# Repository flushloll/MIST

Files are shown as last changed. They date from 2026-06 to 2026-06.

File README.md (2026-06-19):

# MIST
MIST is a robot in the form of a rice-cooker with legs, originating from the Pantheon Show. Our goal in this project was to test our skills whilst making something beautiful. 

This is our Zine for fallout hackathon:
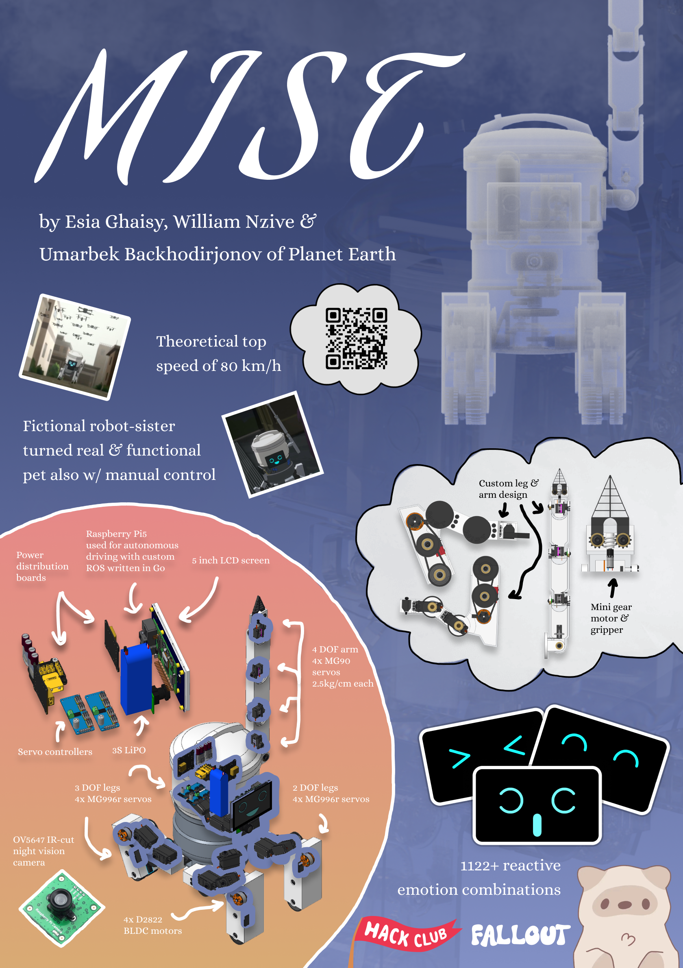
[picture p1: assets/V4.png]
Zine


This zine is the original one. (We left it here because we really liked the design and believed it deserves to be in readme at least)
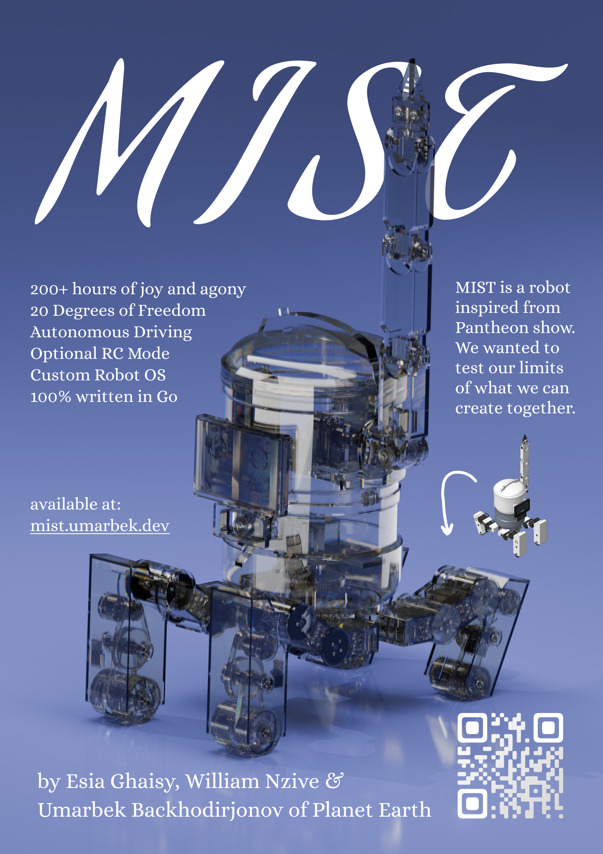
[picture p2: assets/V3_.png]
Zine 2


## Replication
All of the instructions on recreating MIST to keep as a speedy robot pet for yourself are provided below.

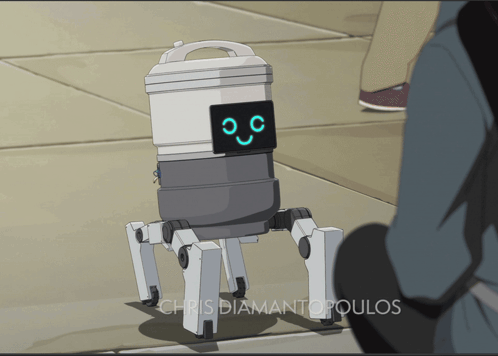
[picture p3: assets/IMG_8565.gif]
mist_gif


### Software

#### 1. Operating System
We've chosen DietPi due to its stability and in order to maximise available resources by ditching the GUI. It would be preferarble to flash some ssd instead of a flash card for reliability. In installation of the DietPi on the raspberry pi, we must choose to install these programs: tailscale, openssh, go.

#### 2. Remote control with Tailscale (optional but recommended)
```bash
# Authentication
tailscale up

# Port Forwarding
echo 'net.ipv4.ip_forward = 1' | sudo tee -a /etc/sysctl.conf 
echo 'net.ipv6.conf.all.forwarding = 1' | sudo tee -a /etc/sysctl.conf
sudo sysctl -p

# Once you've connected your pi to the network, you can ssh into it from your personal computer with these commands:
ssh username@tailscale-ip
# You can also use device name given or chosen in tailscale:
ssh username@device-name
```

#### 3. Adding GOPATH to $PATH
```bash
# 
nano ~/.bashrc

# Write these into the file:
export GOPATH=$HOME/go
export PATH="$PATH:$GOPATH/bin"
# Exit nano, and save the changes.

# Apply changes
source ~/.bashrc
```

#### 4. Installing text to voice (espeak)
```bash
# Configure audio drivers:
dietpi-config
# > Select '2: Audio Options'
# > For the 'Sound card', select 'rpi-bcm2835-hdmi' or 'usb-dac' depending on your speaker.

# Install text to speech module:
apt update
sudo apt install espeak-ng -y
```

#### 6. Setting up ollama (embeddinggemma)
```bash
# Install Ollama
sudo apt-get install zstd
curl -fsSL https://ollama.com/install.sh | sh

# Get the model
ollama pull embeddinggemma
```

#### 7. Setting up mist-os
Note that mist-os isn't an actual operating system, but rather just a program.
```bash
# Install mist-os:
go install https://github.com/flushloll/MIST/mist-os/main.go

# Run mist-os:
mist-os

# Stop:
Ctrl + C
```

Optional: If you wish to start mist-os after boot automatically:
```bash
# Find where mist-os is installed:
which mist-os
# > Please remember the path or save it to clipboard

# Open Configuration menu:
dietpi-autostart
# > Select "Custom script (background, no autologin)"
# > Press OK
# DietPi should automatically open an editable text file, otherwise open it:
nano /var/lib/dietpi/dietpi-autostart/custom.sh
# > Paste this into the file:
/root/go/bin/mist-os # paste the path given from `which matetra-client` command.
exit 0
# > Save everything, and exit
```

### Hardware

I would suggest assembling the robot by virtue of the subassemblies in the CAD, starting with the smallest and working up to the largest.

An order like this is good:
1. Chunky-Leg
2. Chunky-Leg-2
3. Skinny-Leg
4. Skinny-Leg-2
5. Rice-Cooker-Lower
6. Rice-Cooker-Center
7. Rice-Cooker-Lid
8. Arm

Keep in mind that if a part is not on the BOM then it is a 3D printed part.
Every 3D printed part is printed in PLA except the nylon_heat_brick part which is printed in nylon filament as well as the small_sleeve_1, small_sleeve_2, big_sleeve_1, and big_sleeve_2 parts which are printed in SEBS filament.

Remember to assemble the electronics and hardware as you go through this order. Everything you need to know to assemble MIST succesfully is on the CAD model.

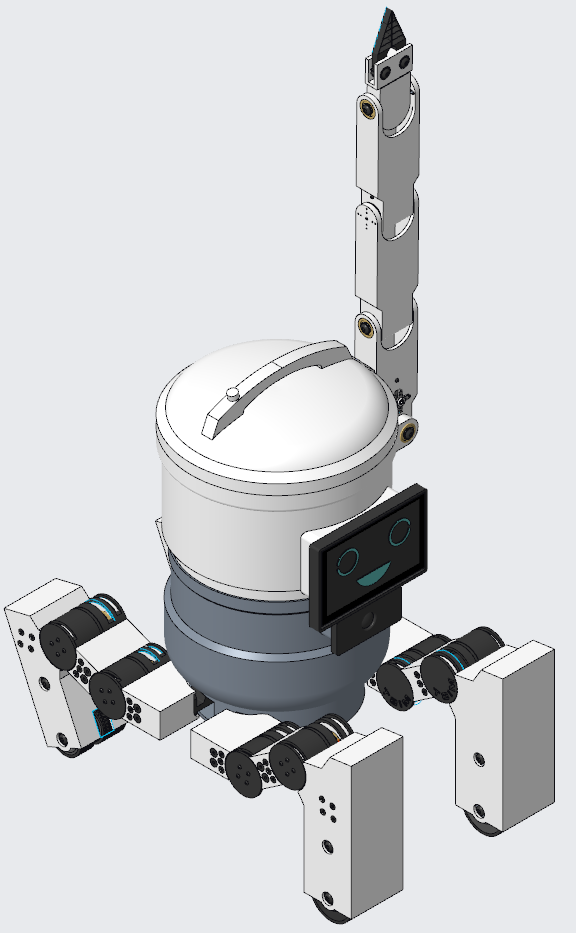
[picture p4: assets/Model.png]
Model

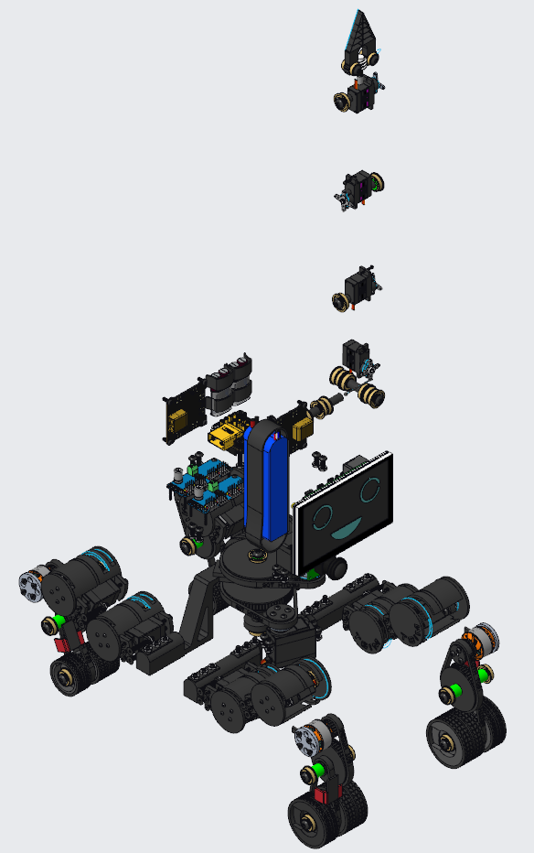
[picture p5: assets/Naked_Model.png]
Naked Model


## 1. BOM - Bill of Materials

<h3><a href="/BOM.pdf">BOM PDF</a></h3>

<h3><a href="BOM.csv">BOM CSV</a></h3>

#### 2. Electronics Wiring Guide

Here are the schematics for wiring MIST. When actually wiring MIST physically, consider where you place your wires and ensure no wires will be pinched or sliced. Use mounting tape to secure your wires onto MIST's chassis and use electrical tape and shrink tubing to cover exposed wires.

If you have questions on how to perform certain electrical tasks such as soldering, crimping, using shrink tube & electrical tape, cutting wire, and just splicing wire in general then please research how to do so before working on MIST. MIST can produce currents capable of setting fire or frying electronics. If you are unsure of how to manage these currents through programming then it would be wise to integrate physical fuses in between electronics to prevent accidents. When deciding on where fuses can be integrated in your circuit consider the maximum current passing through a segment and use that number to decide on the current limit of your fuse. [Here's a good starting point on how to get started with fuses:](https://community.element14.com/technologies/experts/w/documents/27978/a-comprehensive-guide-to-fuses)

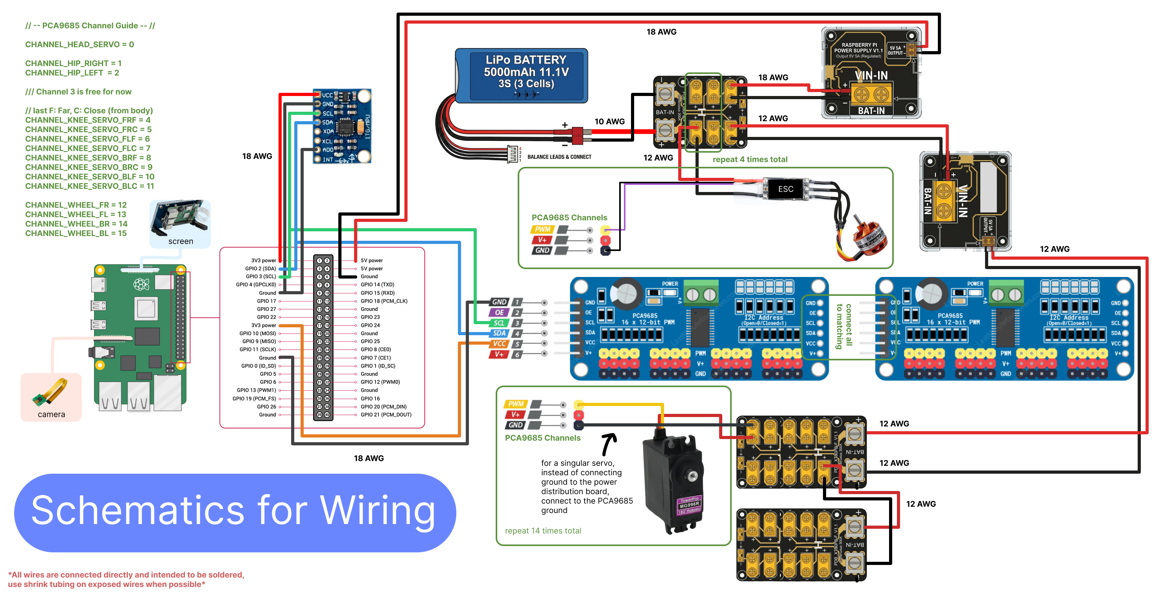
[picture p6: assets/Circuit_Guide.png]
Circuit Guide


#### 3. Enable I2C & Components Test
```zsh
# Open the configuration menu:
dietpi-config
# > Navigate to 'Advanced Options',
# > Ensure 'I2C state' is selected as 'On',
# > Ensure 'I2C frequency' is set to 100 kHz,
# > Exit and reboot the raspberry pi.

# To see if your IMU module is connected, run:
sudo i2cdetect -y 1
# 0x4b is IMU
# ____ is PCA9685
```

# Contribute
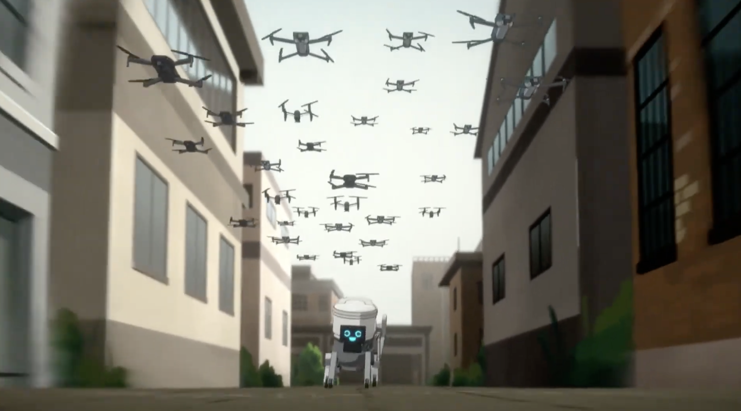
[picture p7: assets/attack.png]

### Realtime file sync between devices
In order to sync files between devices in real-time:
```bash
rsync -avz /path/to/local/dir/ username@remote_ip:/path/to/remote/dir/
```
### Fancy eye
If there is extra time to spend, creating a custom font for fancy-<character> eye type for the screen module would be worth it.

### Questionable arm design?
The servo controlling lateral movement of the arm should be reinforced in future iterations, with both a more powerful servo and thicker bungee cord. With ultra-lightweight printing the current version works hypothetically but it's questionable.

### Head rotation
A mechanism to turn the head and rotate the screen around the body as a result would further contribute toward MIST's accuracy to the show and would be an interesting upgrade.

### Joint improvements
Additional revisions of the joints could likely be made using DC motors with encoders rather than servos to use space more efficiently and result in a more accurate replica of MIST from Pantheon.

### Custom Electronics Solutions
Custom designed ESCs and UBECs are some options of the custom electronics we could develop to reduce project cost.

### Budget Improvements
MIST could be made cheaper overall by reducing the amount of motors/materials used overall. This solution is over-engineered to an extent.

# Math

## Servo quantity and strength

### • How many servos do we need and how strong do they need to be to support the robot?

The robot is being supported by four legs. We can distribute the load between these 4 legs.

If we modestly assume our robot is 7 KG in weight, then each leg should be able to comfortably support 1.75 KG of weight. As such, the stall torque of the motor maintaining the position of each leg should be 4X that so that we are consistently operating at around 33% of each motor’s stall torque.

So, the motors for each leg should be rated for 5.25 KG of weight.

Then, assuming the length of the lever is 18 CM (so each leg is 18 CM long), the motor should (optimally) be rated for [94.25 KG/xCM] so that at 18 CM we can achieve this physical state and be able to support 5.25 KG at the longest point of lever (so the end of the leg)

If we assume this load can be distributed between the eight joints in the robot (2 joints in each of the 4 legs), each motor should be able to support at least 11.78125 kg/cm.

## DC motor quantity and strength

### • How many DC motors do we need and how strong do they need to be to continuously accelerate the robot until an acceptable speed?

Coefficient of friction: ~0.6 (SEBS TPE against asphalt)
Normal force = (7kg * gravity)/4 = 17.1675 N (mg/4)

Frictional force = coefficient of friction * normal force
Frictional force = (0.6 * 17.1675 N) = 10.3005 N

Divided by 4 as load is shared between each wheel

P = F * v
260W = 10.3005 N * 25.24 m/s (minimum to gain traction and overcome stalling force against asphalt at motor maximum power draw)

2 inch diameter wheels

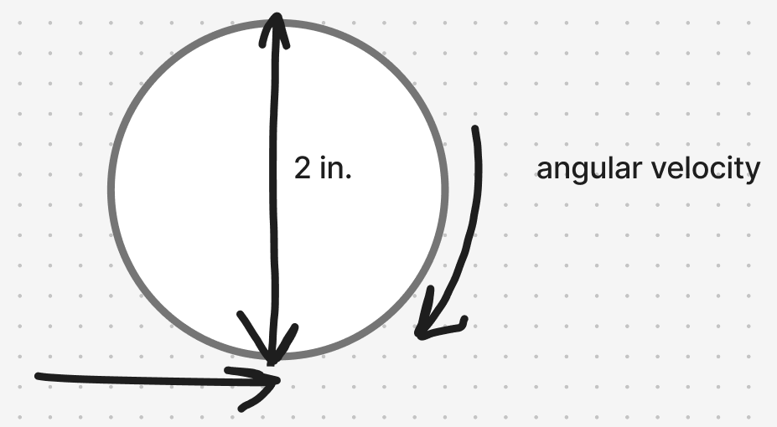
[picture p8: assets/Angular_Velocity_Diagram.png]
Angular Velocity Diagram


Moment of frictional force = perpendicular distance (lever length) * frictional force (10.3005 N)

In this case the perpendicular distance is just the radius of the wheel at 1 inch, so moment of frictional force
(otherwise known as torque) is equal to: 10.3005 N * 1 in.

Which is equal to 10.3005 N * 0.0254 meters, and thus our torque required to begin accelerating on
asphalt is 0.261 newton metres.

Now to calculate angular velocity at this theoretical minimum torque + maximum speed combo
angular velocity = velocity/radius = (25.24 m/s)/(0.0254 m) = 993.7 radians per second

To a more standard motor format, that is 9,489.14 RPM.

Now that we know both the theoretical minimum torque and theoretical maximum speed possible at our power output (260 watts).
we can determine the gear ratio we’d use for our amount of force.

[Selected Motor](https://www.flashhobby.com/d2822-fixed-wing-motor.html)
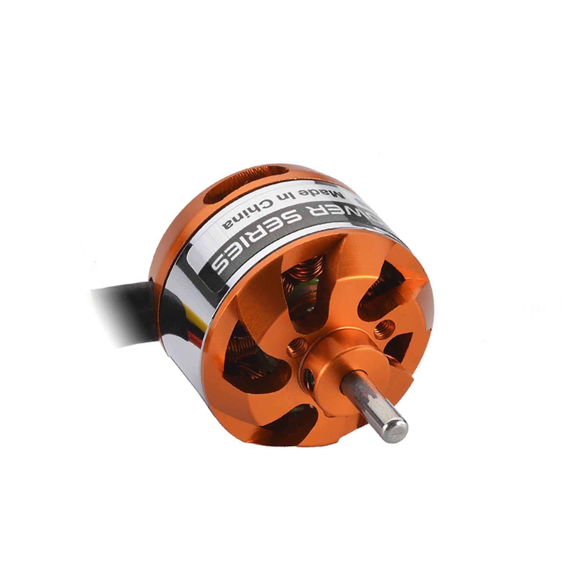
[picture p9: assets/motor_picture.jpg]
Motor_Image

Motor_KV

2600kV * 12v = 312000 RPM

With our given motor RPM immediately off the shelf (31200 RPM) and our theoretical maximum speed possible (9489 RPM) we know
that we must use a 3.288:1 gear reduction to even begin accelerating. Accounting for energy transmission inefficiencies (3.29/0.90)
that increases to 3.66:1 and accounting for the fact that the motor will never always be running at it’s maximum power draw, and will
be running more often than not at ~80% efficiency, we must 3.66/0.8, giving us 4.575:1.

At this ratio, our 31200 RPM becomes 6819.67213115 RPM.

When calculating the surface area speed of our wheels, we learn that our robot can move at a theoretical top speed of 18.14 m/s
Or, in other units: 65.304 km/h at 832 watts

With our smaller diameter wheels (1.416 inches), we must calculate the new angular velocity (25.24/0.018 m) = 1403.53 rad/s = 13,402.75 rpm

Following the same gear ratio calculation as above our gear ratio on our smaller wheels will be 3.23:1

# Fallout Journal

[Check out our fallout journal on the fallout.hackclub.com website :D](https://fallout.hackclub.com/projects/2463)

[Or on our github](assets/mist-journal_current.md)

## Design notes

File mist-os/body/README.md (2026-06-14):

# Body
The purpose of this module is to provide a higher-level control over the actuators in MIST's body rather than individual motor control of her body. The modes offered: **Ride**, which treats MIST as a fancy car, and **Stand**, which allows for precise control of each limb.
Whether this will be the interface provided to the robot ai, is still undecided.
The controls are robot-relative. 
The ride-drone movement style will be used. (below for more.)

## Roadmap:
Done:
1. Head rotation - singular servo
2. Motors only - car-styled movement
To Do:
3. Servos - manual control
3. Servos - automatic height 
4. Servos - automatic tilt
3. Servos - automatic Ride
5. Hand - Forward Kinematics
6. Hand - Inverse Kinematics

## What we have:
Currently, I have established the protocol for controlling each motor in MIST (a physical twin of the cute rice-cooker robot from pantheon). The main issue/uncertainty comes from how should the commands from ps5 controller be interpreted in what ways by the robot.
MIST has:
- head rotation with a servo 180 degrees (pan)
- 4 motors on each of the legs
- 8 servos (2 per leg) in the same axis, that act more as emotional points, and can tilt head I suppose?
- There is some sort of pan mechanism for legs of which I'm still unsure, so it should be decided upon on tomorrow.
- For now, assumption is, we can rotate the front legs by 30-40 degrees each.

## Proposed type of controls:
- Ride-car: There's one axis on a controller responsible for the speed and rotation of controller 
- Ride-rocket: As if MIST is in space and at the end of her back legs, there are thrusters of which intensity we can control. The R2 and L2 control how much thrust is in right and left sides respectedly. The possible downside might be instability (wobbling right and left), we might need to add thretholds of difference between the two sides.
- Ride-tank: R3 and L3 control MIST is similar way, but now we can also do things like 360 rotation on spot by moving one joystick forward and second backward. Same downside as ride-rocket?
- Ride-drone: L3 controls the direction of the robot. (There will be some blind spots on the right and left sides but everything except that should be covered.) R3 controls the rotation in place (right/left) and height of the head. The question would be on how to handle input from both controls simultaneously. 

DJI mavic mini:
Left Stick: Up down, Spin around
Right Stick: Forward, backward, right, left

## Ride Drone Controls (chosen)
R3:
- forward-backward (from 1 to -1): movement, riding in that direction
- right/left tilt: rotation on place (left back right forward and wise-versa)
L3:
- forward-backward: up-down (controlled from the servos on knees)
- right/left: turning (forward legs turn up to 30 degrees right/left, like in a car)
Emergent:
- tilt of the robot is calculated from the MIST's accelerometer readings
(Gemini wrote a simulation from which my brother and I have tested the controls, and it seems to be perfect!)

## Knee structure:
The L-chape connects to a cylindrical main rice-cooker body, and it connects as described. (The last multiple links is just the chape of the last joint.) TLDR: we have: [body]-[servo]-[short segment]-[servo]-[line and then vertical segment, like reverse L, with the wheel on the bottom]
The close one is the one near the body and faris the further out.
It is in a serial arm style.
I am unsure on the angle right now, let's assume it is at 90 degrees when its straight (everything is horizontal so we get a shape like -[]-[]-| and it can go like 90 degrees on each direction? (let's define the limits as constants in the beginning of the file, so we can calibrate it later, so: rest point, max and min.)

## Hand module (ToDo)
Still unsure, need to hear back from William, but I hypothesize this:
The arm has 4 servos:
- 1 inside of the arm, rotating it forward and backward.
- 1 horizontally in the same plane as the one inside, but rotating right and left (left-down and up-right to be concise)
- 3 in the joints for forward-backward movement
- 1 motor to pinch the claw
I will for now ignore the hand module, working on everythign else in assembling the body.

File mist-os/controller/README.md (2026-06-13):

# Controller
This is a component that abstracts PS5 controller movements into simple package.

Usage guide:
```go
package main

import (
	"fmt"
	"mist-os/controller"
	"time"
)

func main() {
	controller, _ := controller.NewController()
	defer controller.Close()
	for {
		controller.Update()
		if controller.CROSS.Pressed { // all of the buttons and axis are in Controller struct.
			fmt.Printf("CROSS is hled down %v\n", time.Now())
		}
	}
}
```

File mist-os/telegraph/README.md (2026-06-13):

# Morse
This module allows to use a Button from a Controller as a telegraph, converting morse code into text, that can be used as commands.

Usage guide:
```go
package main

import (
	"mist-os/controller"
	"mist-os/telegraph"
	"time"
)

func main() {
	controller, _ := controller.NewController()
	defer controller.Close()

	telegraph := telegraph.NewTelegraph(&controller.CIRCLE)

	for {
		controller.Update()
		telegraph.Tick()
		telegraph.Execute()
		time.Sleep(10 * time.Millisecond)
	}
}
```

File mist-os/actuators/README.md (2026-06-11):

# Actuators
This is a module responsible for all of the servos and brushless motors that make up MIST.

!TODO: Insert Servo (part of MIST) to Index Mapping Diagram

Usage guide:
```go
package main

import (
	"fmt"
	"log"
	"mist-os/actuators"
	"time"
)

func main() {
	// setup
	cntr, err := actuators.NewController()
	if err != nil {
		log.Fatal(err)
	}
	defer cntr.Close()

	// Servos:
	// move servo 0 to center position
	cntr.SetServo(0, 90)

	// smoothly move servo 1 from 0 to 180
	for angle := 0.0; angle <= 180; angle += 10 {
		cntr.SetServo(1, angle)
		time.Sleep(50 * time.Millisecond)
	}

	// Motors:
	// warming esc's
	for ch := 12; ch <= 15; ch++ {
		if err := cntr.ArmESC(ch); err != nil {
			log.Fatalf("failed to arm channel %d: %w", ch, err)
		}
	}
	fmt.Println("ESCs armed.")

	// spin motor on channel 12 up slowly then back down
	for throttle := 0.0; throttle <= 0.5; throttle += 0.1 {
		cntr.SetThrottle(12, throttle)
		time.Sleep(200 * time.Millisecond)
	}
	cntr.SetThrottle(12, 0)
}
```

## Connections:
PCA9685 to RP5:
- 1GND to 25Ground
- 3SCL to 5SCL(GPIO3)
- 4SDA to 3SDA(GPIO2)
- 5VCC to 17 3V3 power
PCA9685 to Actuators:
- 12 slots of 9,10,11 for TowerPro MG996R 180 degree servos.
- 4 slots of 9.10,11 for DYS D2822 Brushless Outrunner Motor 2-3S for Multicopter RC Aircraft Fixed-Wing UAV（D2822 1800KV）controlled by 5A/5A PRO/10A/20A/30A/40A/50A/60A/120A Dual Way Bidirectional Brushed ESC Control For Rc Model Boat/tank 180-795 Brushed Motor.

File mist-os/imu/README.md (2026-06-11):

# IMU
Comprehensive package to work with the IMU module. It can both give one-time readings as well as stream data. It operates in SI units, but you can get arbitary raw sensor readings as well.

MIST's IMU module: MPU-6050

Usage guide:
```go
package main

import (
	"fmt"
	"log"
	"mist-os/imu"
	"time"
)

func main() {
	sensor, err := imu.New()
	if err != nil {
		log.Fatal("imu initialisation error: %w", err)
	}
	defer sensor.Close()

	for {
		data, err := sensor.Read()
		if err != nil {
			fmt.Print("imu read error: %w", err)
			continue
		}

		fmt.Printf("Pitch: %.1f | Roll: %1.f | Temp: %.1f",
			data.Pitch(), data.Roll(), data.Temperature)
		time.Sleep(10 * time.Millisecond)
	}
}
```

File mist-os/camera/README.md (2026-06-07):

# Camera
For testing purposes, there are both Mac's and actual MIST's camera implementations.
This package exposes a function `Shoot()`, which when called returns an `image.Image` from the camera module.

MIST's camera module: Raspberry Pi 5 Camera 5MP 1080P Optional Night Vision Wide Angle IR-CUT FF AF Cameras for RPI 5 Pi5 Zero | FF 69

Usage guide:
```go
package main

import (
 "mist-os/screen"
)

func main() {
 cam, _ := camera.NewCamera(0)
 defer cam.Close()
 imageBytes, _ := cam.Shoot()
 os.WriteFile("test_capture.png", imageBytes, 0644)
}
```

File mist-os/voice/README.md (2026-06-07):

# Voice
Raspberry Pi doesn't have a build-in speaker, but USB/Bluetooth speaker should do.

Example usage:
```go
package main

import (
	"mist-os/voice"
)

func main() {
	voice := voice.NewVoiceModule()
	voice.Speak("Hello, I am MIST. My voice system is now operational.", "en+f5", 100, 150)
	for {

	}
}
```

Promising Voices for Mac:
- Karen
- Kyoko
- Meijia
- Melina
- Moira
- Ona
- Samantha
- Tina
- Yuna

Promising Voice for Linux:
speak-ng -v en+f4 -p 125 "There are some people who would like to create, dream" -w morning4.wav

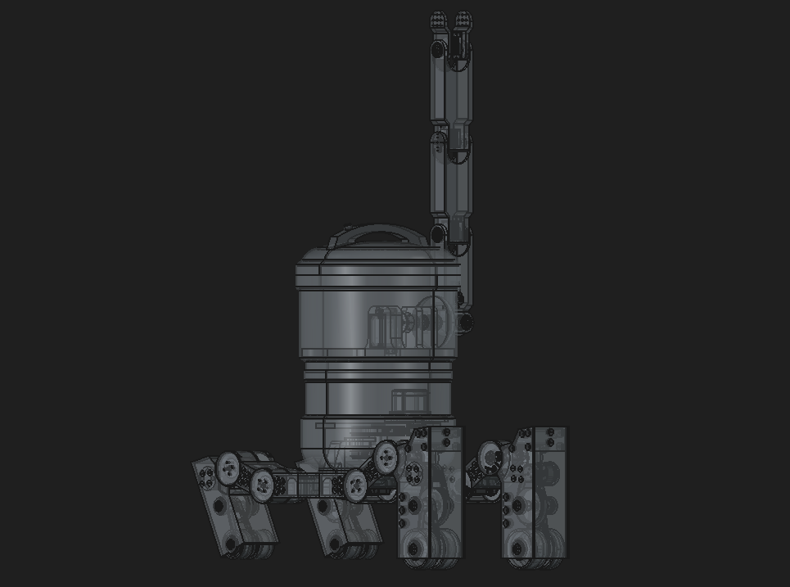
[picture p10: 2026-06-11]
assets/ccd2b67adb1f2e972bdda4df0c3afa52f13996bc6b8d59f18e003bfad196b90e.png

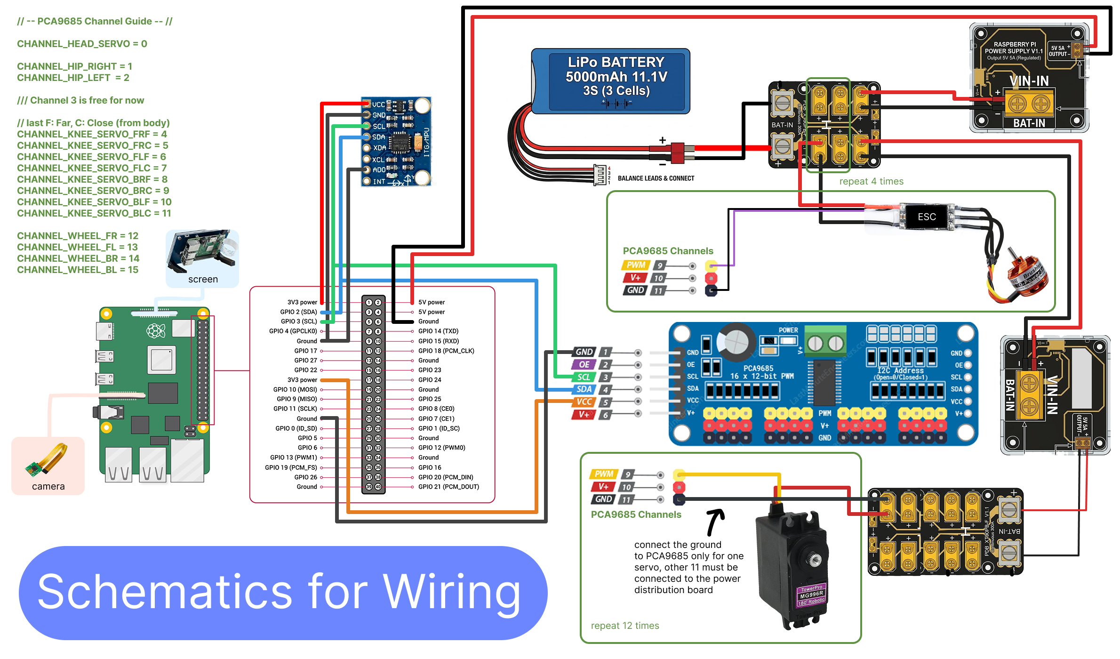
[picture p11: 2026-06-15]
assets/cf93e6d5dc4156bd0e512205f6ad03fc0436a38a9b7ac233e9a3aa5704771bca.png

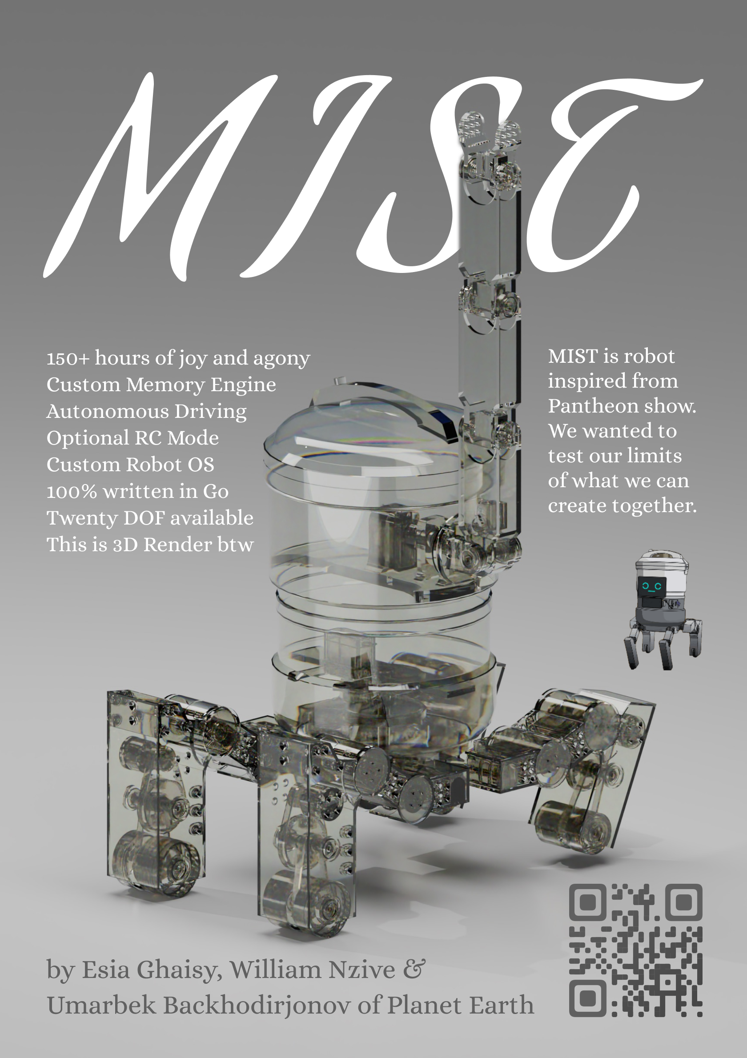
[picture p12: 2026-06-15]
assets/dc4bebfd2665ba8eb09146e643a19c9611d8cfe4fb39f6bc9c8c37b82709efe4.png

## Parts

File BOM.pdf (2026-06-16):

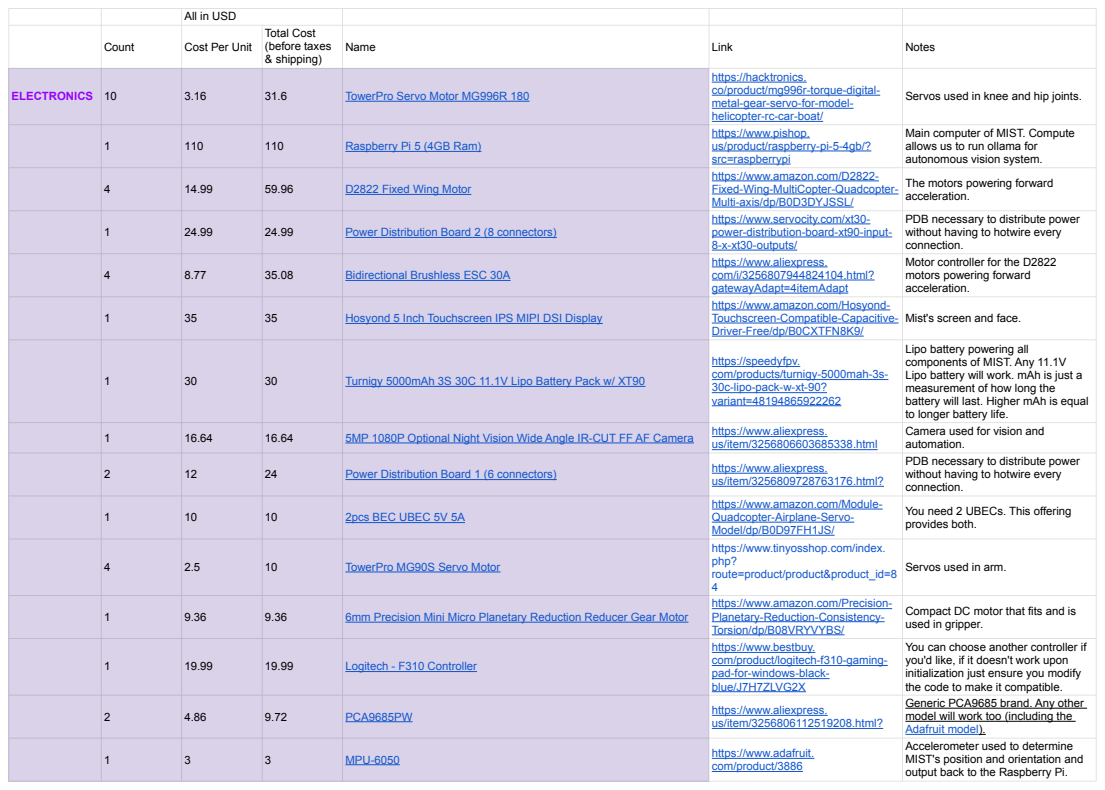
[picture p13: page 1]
Count; Cost Per Unit; Total Cost (before taxes & shipping); Name; Link; Notes; ELECTRONICS 10; TowerPro Servo Motor MG996R 180; Raspberry Pi 5 (4GB Ram); D2822 Fixed Wing Motor; Power Distribution Board 2 (8 connectors); Bidirectional Brushless ESC 30A; Hosyond 5 Inch Touchscreen IPS MIPI DSI Display; Turnigy 5000mAh 3S 30C 11.1V Lipo Battery Pack w/ XT90; 5MP 1080P Optional Night Vision Wide Angle IR-CUT FF AF Camera; https://www.aliexpress.; Power Distribution Board 1 (6 connectors)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

All in USD

https://hacktronics.
co/product/mg996r-torque-digital-
metal-gear-servo-for-model-
helicopter-rc-car-boat/ (https://hacktronics.co/product/mg996r-torque-digital-metal-gear-servo-for-model-helicopter-rc-car-boat/)
https://www.pishop.
us/product/raspberry-pi-5-4gb/?
src=raspberrypi (https://www.pishop.us/product/raspberry-pi-5-4gb/?src=raspberrypi)
https://www.amazon.com/D2822-
Fixed-Wing-MultiCopter-Quadcopter-
Multi-axis/dp/B0D3DYJSSL/ (https://www.amazon.com/D2822-Fixed-Wing-MultiCopter-Quadcopter-Multi-axis/dp/B0D3DYJSSL/)
https://www.servocity.com/xt30-
power-distribution-board-xt90-input-
8-x-xt30-outputs/ (https://www.servocity.com/xt30-power-distribution-board-xt90-input-8-x-xt30-outputs/)
https://www.aliexpress.
com/i/3256807944824104.html?
gatewayAdapt=4itemAdapt (https://www.aliexpress.com/i/3256807944824104.html?gatewayAdapt=4itemAdapt)
https://www.amazon.com/Hosyond-
Touchscreen-Compatible-Capacitive-
Driver-Free/dp/B0CXTFN8K9/ (https://www.amazon.com/Hosyond-Touchscreen-Compatible-Capacitive-Driver-Free/dp/B0CXTFN8K9/?th=1)

Servos used in knee and hip joints.

Main computer of MIST. Compute
allows us to run ollama for
autonomous vision system.

The motors powering forward
acceleration.

PDB necessary to distribute power
without having to hotwire every
connection.
Motor controller for the D2822
motors powering forward

Mist's screen and face.

Lipo battery powering all
components of MIST. Any 11.1V
Lipo battery will work. mAh is just a
measurement of how long the
battery will last. Higher mAh is equal
to longer battery life.
Camera used for vision and
automation.

https://speedyfpv.
com/products/turnigy-5000mah-3s-
30c-lipo-pack-w-xt-90?
variant=48194865922262 (https://speedyfpv.com/products/turnigy-5000mah-3s-30c-lipo-pack-w-xt-90?variant=48194865922262)

us/item/3256806603685338.html (https://www.aliexpress.us/item/3256806603685338.html)

us/item/3256809728763176.html? (https://www.aliexpress.us/item/3256809728763176.html?)

https://www.amazon.com/Module-
Quadcopter-Airplane-Servo-
Model/dp/B0D97FH1JS/ (https://www.amazon.com/Module-Quadcopter-Airplane-Servo-Model/dp/B0D97FH1JS/)
https://www.tinyosshop.com/index.
php?
route=product/product&product_id=8
https://www.amazon.com/Precision-
Planetary-Reduction-Consistency-
Torsion/dp/B08VRYVYBS/ (https://www.amazon.com/Precision-Planetary-Reduction-Consistency-Torsion/dp/B08VRYVYBS/)
https://www.bestbuy.
com/product/logitech-f310-gaming-
pad-for-windows-black-
blue/J7H7ZLVG2X (https://www.bestbuy.com/product/logitech-f310-gaming-pad-for-windows-black-blue/J7H7ZLVG2X)

You need 2 UBECs. This offering
provides both.

Servos used in arm.

Compact DC motor that fits and is
used in gripper.

You can choose another controller if
you'd like, if it doesn't work upon
initialization just ensure you modify
the code to make it compatible.
Generic PCA9685 brand. Any other
model will work too (including the
Adafruit model).
Accelerometer used to determine
MIST's position and orientation and
output back to the Raspberry Pi.

us/item/3256806112519208.html? (https://www.aliexpress.us/item/3256806112519208.html?)

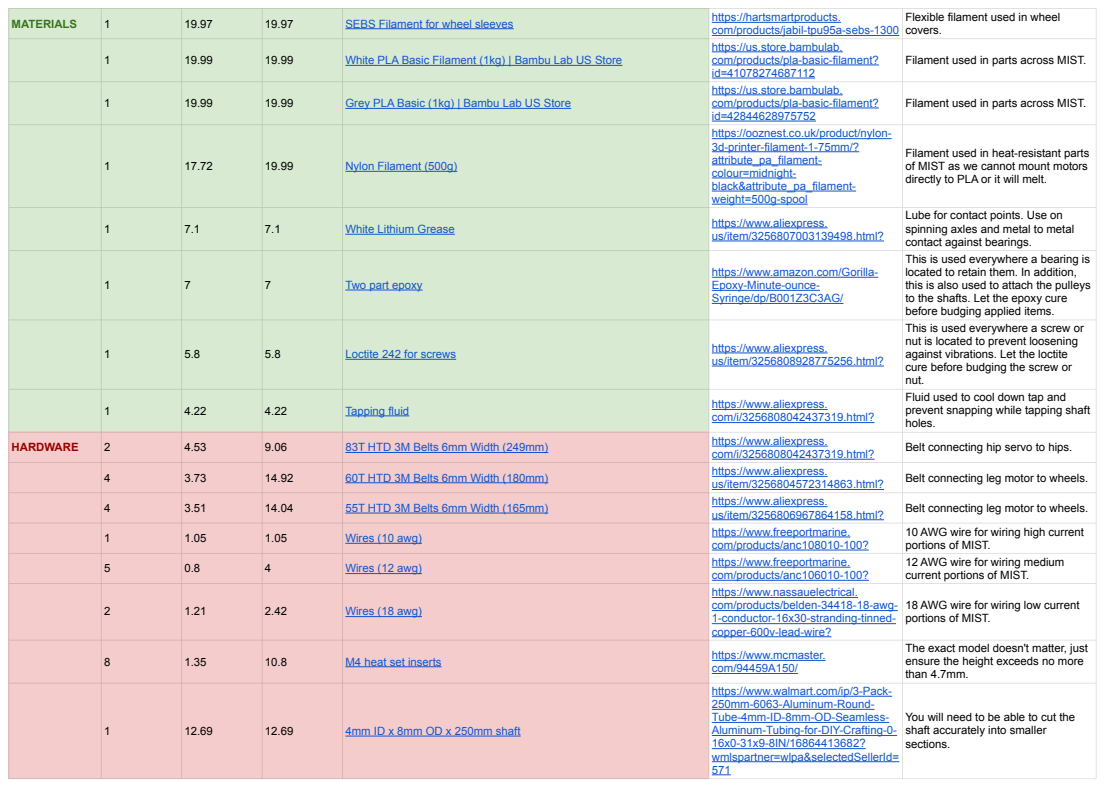
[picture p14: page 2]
MATERIALS; SEBS Filament for wheel sleeves; https://hartsmartproducts.; White PLA Basic Filament (1kg) | Bambu Lab US Store; Grey PLA Basic (1kg) | Bambu Lab US Store; Nylon Filament (500g); White Lithium Grease; https://www.aliexpress.; Two part epoxy; Loctite 242 for screws; Tapping fluid; com/i/3256808042437319.html?; HARDWARE; 83T HTD 3M Belts 6mm Width (249mm); Belt connecting hip servo to hips.; 60T HTD 3M Belts 6mm Width (180mm); us/item/3256804572314863.html?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

Flexible filament used in wheel
covers.

com/products/jabil-tpu95a-sebs-1300 (https://hartsmartproducts.com/products/jabil-tpu95a-sebs-1300)
https://us.store.bambulab.
com/products/pla-basic-filament?
https://ooznest.co.uk/product/nylon-
3d-printer-filament-1-75mm/?
attribute_pa_filament-
colour=midnight-
black&attribute_pa_filament-
weight=500g-spool (https://ooznest.co.uk/product/nylon-3d-printer-filament-1-75mm/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)

Filament used in parts across MIST.

Filament used in heat-resistant parts
of MIST as we cannot mount motors
directly to PLA or it will melt.

Lube for contact points. Use on
spinning axles and metal to metal
contact against bearings.
This is used everywhere a bearing is
located to retain them. In addition,
this is also used to attach the pulleys
to the shafts. Let the epoxy cure
before budging applied items.
This is used everywhere a screw or
nut is located to prevent loosening
against vibrations. Let the loctite
cure before budging the screw or
nut.
Fluid used to cool down tap and
prevent snapping while tapping shaft
holes.

us/item/3256807003139498.html? (https://www.aliexpress.us/item/3256807003139498.html?)

https://www.amazon.com/Gorilla-
Epoxy-Minute-ounce-
Syringe/dp/B001Z3C3AG/ (https://www.amazon.com/Gorilla-Epoxy-Minute-ounce-Syringe/dp/B001Z3C3AG/)

us/item/3256808928775256.html? (https://www.aliexpress.us/item/3256808928775256.html?)

10 AWG wire for wiring high current
portions of MIST.
12 AWG wire for wiring medium
current portions of MIST.

com/products/anc106010-100? (https://www.freeportmarine.com/products/anc106010-100?)
https://www.nassauelectrical.
com/products/belden-34418-18-awg-
1-conductor-16x30-stranding-tinned-
copper-600v-lead-wire? (https://www.nassauelectrical.com/products/belden-34418-18-awg-1-conductor-16x30-stranding-tinned-copper-600v-lead-wire)

18 AWG wire for wiring low current

The exact model doesn't matter, just
ensure the height exceeds no more
than 4.7mm.

https://www.walmart.com/ip/3-Pack-
250mm-6063-Aluminum-Round-
Tube-4mm-ID-8mm-OD-Seamless-
Aluminum-Tubing-for-DIY-Crafting-0-
wmlspartner=wlpa&selectedSellerId=

You will need to be able to cut the
shaft accurately into smaller
sections.

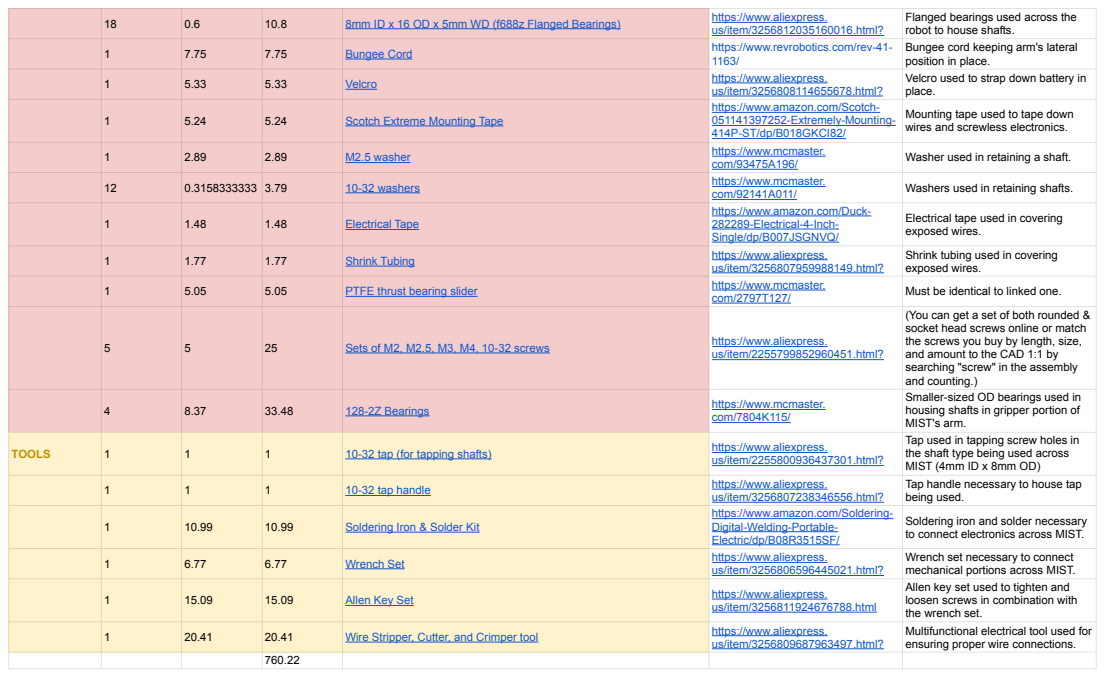
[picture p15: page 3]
8mm ID x 16 OD x 5mm WD (f688z Flanged Bearings); https://www.aliexpress.; Bungee Cord; https://www.revrobotics.com/rev-41-; Velcro; Scotch Extreme Mounting Tape; M2.5 washer; https://www.mcmaster.; com/93475A196/; Washer used in retaining a shaft.; 10-32 washers; com/92141A011/; Washers used in retaining shafts.; Electrical Tape; Shrink Tubing; PTFE thrust bearing slider; com/2797T127/; Must be identical to linked one.; Sets of M2, M2.5, M3, M4, 10-32 screws; 128-2Z Bearings; com/7804K115/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

Flanged bearings used across the
robot to house shafts.
Bungee cord keeping arm's lateral
position in place.
Velcro used to strap down battery in
place.

us/item/3256812035160016.html? (https://www.aliexpress.us/item/3256812035160016.html?)

us/item/3256808114655678.html? (https://www.aliexpress.us/item/3256808114655678.html?)
https://www.amazon.com/Scotch-
051141397252-Extremely-Mounting-
414P-ST/dp/B018GKCI82/ (https://www.amazon.com/Scotch-051141397252-Extremely-Mounting-414P-ST/dp/B018GKCI82/)

Mounting tape used to tape down
wires and screwless electronics.

https://www.amazon.com/Duck-
282289-Electrical-4-Inch-
Single/dp/B007JSGNVQ/ (https://www.amazon.com/Duck-282289-Electrical-4-Inch-Single/dp/B007JSGNVQ/)

Electrical tape used in covering
exposed wires.

Shrink tubing used in covering

us/item/3256807959988149.html? (https://www.aliexpress.us/item/3256807959988149.html?)

(You can get a set of both rounded &
socket head screws online or match
the screws you buy by length, size,
and amount to the CAD 1:1 by
searching "screw" in the assembly
and counting.)
Smaller-sized OD bearings used in
housing shafts in gripper portion of
MIST's arm.
Tap used in tapping screw holes in
the shaft type being used across
MIST (4mm ID x 8mm OD)
Tap handle necessary to house tap
being used.

us/item/2255799852960451.html? (https://www.aliexpress.us/item/2255799852960451.html?)

us/item/2255800936437301.html? (https://www.aliexpress.us/item/2255800936437301.html?)

us/item/3256807238346556.html? (https://www.aliexpress.us/item/3256807238346556.html?)
https://www.amazon.com/Soldering-
Digital-Welding-Portable-
Electric/dp/B08R3515SF/ (https://www.amazon.com/Soldering-Digital-Welding-Portable-Electric/dp/B08R3515SF/)

Soldering iron and solder necessary
to connect electronics across MIST.

Wrench set necessary to connect
mechanical portions across MIST.
Allen key set used to tighten and
loosen screws in combination with
the wrench set.
Multifunctional electrical tool used for
ensuring proper wire connections.

us/item/3256806596445021.html? (https://www.aliexpress.us/item/3256806596445021.html?)

us/item/3256811924676788.html (https://www.aliexpress.us/item/3256811924676788.html)

us/item/3256809687963497.html? (https://www.aliexpress.us/item/3256809687963497.html?)

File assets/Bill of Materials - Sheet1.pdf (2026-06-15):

All in USD

Count | Cost Per Unit

Total Cost
(before taxes
& shipping)
Name + Link | Notes
ELECTRONICS 10 | 12.1 | 121 | TowerPro Servo Motor MG996R 180 (https://thepihut.com/products/towerpro-servo-motor-mg996r-metal-gear-180)
1 | 110 | 110 | Raspberry Pi 5 (4GB Ram) (https://www.pishop.us/product/raspberry-pi-5-4gb/?src=raspberrypi)
4 | 20 | 80 | D2822 Fixed Wing Motor (https://www.amazon.com/D2822-Fixed-Wing-MultiCopter-Quadcopter-Multi-axis/dp/B0D3DYJSSL)
2 | 24.99 | 49.98 | Power Distribution Board 2 (8 connectors) (https://www.servocity.com/xt30-power-distribution-board-xt90-input-8-x-xt30-outputs/)
4 | 12.02 | 48.08 | Bidirectional Brushless ESC (https://www.aliexpress.com/i/3256807944824104.html?gatewayAdapt=4itemAdapt)
1 | 35 | 35 | Hosyond 5 Inch Touchscreen IPS MIPI DSI Display (https://www.amazon.com/Hosyond-Touchscreen-Compatible-Capacitive-Driver-Free/dp/B0CXTFN8K9)
1 | 30 | 30 | Turnigy 5000mAh 3S 30C 11.1V Lipo Battery Pack w/ XT90 (https://speedyfpv.com/products/turnigy-5000mah-3s-30c-lipo-pack-w-xt-90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)

Any 11.1V Lipo battery will work. mAh is just a measurement of how long the battery will last. Higher mAh is equal to longer battery life.
1 | 16.64 | 16.64 | 5MP 1080P Optional Night Vision Wide Angle IR-CUT FF AF Camera (https://www.aliexpress.us/item/3256806603685338.html?curPageLogUid=L3tBDgOkZJRK)
2 | 12 | 24 | Power Distribution Board 1 (6 connectors)
1 | 10 | 10 | 2pcs BEC UBEC 5V 5A (https://www.amazon.com/Module-Quadcopter-Airplane-Servo-Model/dp/B0D97FH1JS?sp_csd=d2lkZ2V0TmFtZT1zcF9hdGY) | You need 2 UBECs. This offering
provides both.
4 | 2.5 | 10 | TowerPro MG90S Servo Motor (https://www.tinyosshop.com/index.php?route=product/product&product_id=84)
1 | 9.36 | 9.36 | 6mm Precision Mini Micro Planetary Reduction Reducer Gear Motor (https://www.amazon.com/Precision-Planetary-Reduction-Consistency-Torsion/dp/B08VRYVYBS)
1 | 74 | 74 | PS5 Controller (https://www.amazon.com/PlayStation-DualSenseTM-Wireless-Controller-Gaming-Console/dp/B0FY6X2XXY)

You can choose another controller if you'd like, if it doesn't work upon initialization just ensure you modify the code to make it compatible.

1 | 5 | 5 | PCA9685PW (https://www.aliexpress.us/item/3256806112519208.html?curPageLogUid=gDL2pBrAG0Cr)

Generic PCA9685 brand. Any other model will work too (including the Adafruit model).
1 | 3 | 3 | MPU-6050 (https://www.adafruit.com/product/3886)
MATERIALS | 1 | 45.51 | 45.51 | SEBS Filament for wheel sleeves (https://hartsmartproducts.com/products/jabil-tpu95a-sebs-1300?variant=44402264211677&country=US)
1 | 19.99 | 19.99 | White PLA Basic Filament (1kg) | Bambu Lab US Store (https://us.store.bambulab.com/products/pla-basic-filament?id=41078274687112)
1 | 19.99 | 19.99 | Grey PLA Basic (1kg) | Bambu Lab US Store (https://us.store.bambulab.com/products/pla-basic-filament?id=41078274687112)
1 | 17.72 | 19.99 | Nylon Filament (500g) (https://ooznest.co.uk/product/nylon-3d-printer-filament-1-75mm/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)
1 | 7.1 | 7.1 | White Lithium Grease (https://www.aliexpress.us/item/3256807003139498.html?curPageLogUid=4JpSOG6ihT6e)

Lube for contact points. Use on spinning axles and metal to metal contact against bearings.

1 | 7 | 7 | Two part epoxy (https://www.amazon.com/Gorilla-Epoxy-Minute-ounce-Syringe/dp/B001Z3C3AG)

This is used everywhere a bearing is located to retain them. Let the epoxy cure before budging the bearings.

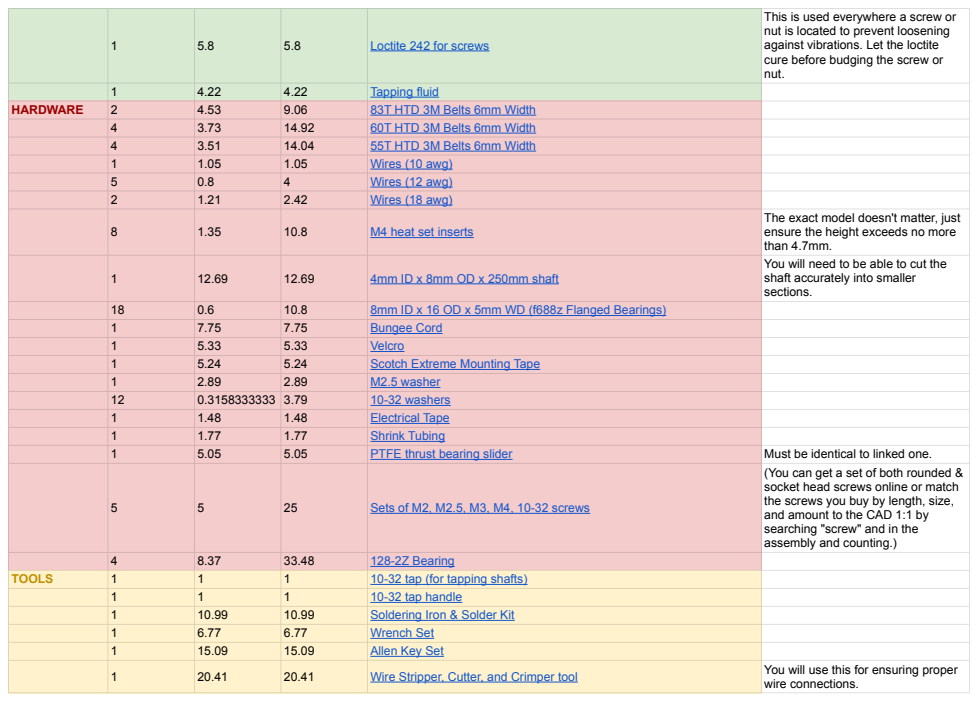
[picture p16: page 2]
Loctite 242 for screws; Tapping fluid; HARDWARE; 83T HTD 3M Belts 6mm Width; 60T HTD 3M Belts 6mm Width; 55T HTD 3M Belts 6mm Width; Wires (10 awg); Wires (12 awg); Wires (18 awg); M4 heat set inserts; 4mm ID x 8mm OD x 250mm shaft; 8mm ID x 16 OD x 5mm WD (f688z Flanged Bearings); Bungee Cord; Velcro; Scotch Extreme Mounting Tape; M2.5 washer; 10-32 washers; Electrical Tape; Shrink Tubing; PTFE thrust bearing slider; Must be identical to linked one.; Sets of M2, M2.5, M3, M4, 10-32 screws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

This is used everywhere a screw or
nut is located to prevent loosening
against vibrations. Let the loctite
cure before budging the screw or
nut.

The exact model doesn't matter, just
ensure the height exceeds no more
than 4.7mm.
You will need to be able to cut the
shaft accurately into smaller
sections.

(You can get a set of both rounded &
socket head screws online or match
the screws you buy by length, size,
and amount to the CAD 1:1 by
searching "screw" and in the
assembly and counting.)

982.48

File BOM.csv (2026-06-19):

 |  | All in USD
 | Count | Cost Per Unit | Total Cost (before taxes & shipping) | Name | Link | Notes
ELECTRONICS | 10 | 3.16 | 31.6 | TowerPro Servo Motor MG996R 180 | https://hacktronics.co/product/mg996r-torque-digital-metal-gear-servo-for-model-helicopter-rc-car-boat/ | Servos used in knee and hip joints.
 | 1 | 110 | 110 | Raspberry Pi 5 (4GB Ram) | https://www.pishop.us/product/raspberry-pi-5-4gb/?src=raspberrypi | Main computer of MIST. Compute allows us to run ollama for autonomous vision system.
 | 4 | 14.99 | 59.96 | D2822 Fixed Wing Motor | https://www.amazon.com/D2822-Fixed-Wing-MultiCopter-Quadcopter-Multi-axis/dp/B0D3DYJSSL/ | The motors powering forward acceleration.
 | 1 | 24.99 | 24.99 | Power Distribution Board 2 (8 connectors) | https://www.servocity.com/xt30-power-distribution-board-xt90-input-8-x-xt30-outputs/ | PDB necessary to distribute power without having to hotwire every connection.
 | 4 | 8.77 | 35.08 | Bidirectional Brushless ESC 30A | https://www.aliexpress.com/i/3256807944824104.html?gatewayAdapt=4itemAdapt | Motor controller for the D2822 motors powering forward acceleration.
 | 1 | 35 | 35 | Hosyond 5 Inch Touchscreen IPS MIPI DSI Display | https://www.amazon.com/Hosyond-Touchscreen-Compatible-Capacitive-Driver-Free/dp/B0CXTFN8K9/ | Mist's screen and face.
 | 1 | 30 | 30 | Turnigy 5000mAh 3S 30C 11.1V Lipo Battery Pack w/ XT90 | https://speedyfpv.com/products/turnigy-5000mah-3s-30c-lipo-pack-w-xt-90?variant=48194865922262 | Lipo battery powering all components of MIST. Any 11.1V Lipo battery will work. mAh is just a measurement of how long the battery will last. Higher mAh is equal to longer battery life.
 | 1 | 16.64 | 16.64 | 5MP 1080P Optional Night Vision Wide Angle IR-CUT FF AF Camera | https://www.aliexpress.us/item/3256806603685338.html | Camera used for vision and automation.
 | 2 | 12 | 24 | Power Distribution Board 1 (6 connectors) | https://www.aliexpress.us/item/3256809728763176.html? | PDB necessary to distribute power without having to hotwire every connection.
 | 1 | 10 | 10 | 2pcs BEC UBEC 5V 5A | https://www.amazon.com/Module-Quadcopter-Airplane-Servo-Model/dp/B0D97FH1JS/ | You need 2 UBECs. This offering provides both.
 | 4 | 2.5 | 10 | TowerPro MG90S Servo Motor | https://www.tinyosshop.com/index.php?route=product/product&product_id=84 | Servos used in arm.
 | 1 | 9.36 | 9.36 | 6mm Precision Mini Micro Planetary Reduction Reducer Gear Motor | https://www.amazon.com/Precision-Planetary-Reduction-Consistency-Torsion/dp/B08VRYVYBS/ | Compact DC motor that fits and is used in gripper.
 | 1 | 19.99 | 19.99 | Logitech - F310 Controller | https://www.bestbuy.com/product/logitech-f310-gaming-pad-for-windows-black-blue/J7H7ZLVG2X | You can choose another controller if you'd like, if it doesn't work upon initialization just ensure you modify the code to make it compatible.
 | 2 | 4.86 | 9.72 | PCA9685PW | https://www.aliexpress.us/item/3256806112519208.html? | Generic PCA9685 brand. Any other model will work too (including the Adafruit model).
 | 1 | 3 | 3 | MPU-6050 | https://www.adafruit.com/product/3886 | Accelerometer used to determine MIST's position and orientation and output back to the Raspberry Pi.
MATERIALS | 1 | 19.97 | 19.97 | SEBS Filament for wheel sleeves | https://hartsmartproducts.com/products/jabil-tpu95a-sebs-1300 | Flexible filament used in wheel covers.
 | 1 | 19.99 | 19.99 | White PLA Basic Filament (1kg) | Bambu Lab US Store | https://us.store.bambulab.com/products/pla-basic-filament?id=41078274687112 | Filament used in parts across MIST.
 | 1 | 19.99 | 19.99 | Grey PLA Basic (1kg) | Bambu Lab US Store | https://us.store.bambulab.com/products/pla-basic-filament?id=42844628975752 | Filament used in parts across MIST.
 | 1 | 17.72 | 19.99 | Nylon Filament (500g) | https://ooznest.co.uk/product/nylon-3d-printer-filament-1-75mm/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 | Filament used in heat-resistant parts of MIST as we cannot mount motors directly to PLA or it will melt.
 | 1 | 7.1 | 7.1 | White Lithium Grease | https://www.aliexpress.us/item/3256807003139498.html? | Lube for contact points. Use on spinning axles and metal to metal contact against bearings.
 | 1 | 7 | 7 | Two part epoxy | https://www.amazon.com/Gorilla-Epoxy-Minute-ounce-Syringe/dp/B001Z3C3AG/ | This is used everywhere a bearing is located to retain them. In addition, this is also used to attach the pulleys to the shafts. Let the epoxy cure before budging applied items.
 | 1 | 5.8 | 5.8 | Loctite 242 for screws | https://www.aliexpress.us/item/3256808928775256.html? | This is used everywhere a screw or nut is located to prevent loosening against vibrations. Let the loctite cure before budging the screw or nut.
 | 1 | 4.22 | 4.22 | Tapping fluid | https://www.aliexpress.com/i/3256808042437319.html? | Fluid used to cool down tap and prevent snapping while tapping shaft holes.
HARDWARE | 2 | 4.53 | 9.06 | 83T HTD 3M Belts 6mm Width (249mm) | https://www.aliexpress.com/i/3256808042437319.html? | Belt connecting hip servo to hips.
 | 4 | 3.73 | 14.92 | 60T HTD 3M Belts 6mm Width (180mm) | https://www.aliexpress.us/item/3256804572314863.html? | Belt connecting leg motor to wheels.
 | 4 | 3.51 | 14.04 | 55T HTD 3M Belts 6mm Width (165mm) | https://www.aliexpress.us/item/3256806967864158.html? | Belt connecting leg motor to wheels.
 | 1 | 1.05 | 1.05 | Wires (10 awg) | https://www.freeportmarine.com/products/anc108010-100? | 10 AWG wire for wiring high current portions of MIST.
 | 5 | 0.8 | 4 | Wires (12 awg) | https://www.freeportmarine.com/products/anc106010-100? | 12 AWG wire for wiring medium current portions of MIST.
 | 2 | 1.21 | 2.42 | Wires (18 awg) | https://www.nassauelectrical.com/products/belden-34418-18-awg-1-conductor-16x30-stranding-tinned-copper-600v-lead-wire | 18 AWG wire for wiring low current portions of MIST.
 | 8 | 1.35 | 10.8 | M4 heat set inserts | https://www.mcmaster.com/94459A150/ | The exact model doesn't matter, just ensure the height exceeds no more than 4.7mm.
 | 1 | 12.69 | 12.69 | 4mm ID x 8mm OD x 250mm shaft | https://www.walmart.com/ip/3-Pack-250mm-6063-Aluminum-Round-Tube-4mm-ID-8mm-OD-Seamless-Aluminum-Tubing-for-DIY-Crafting-0-16x0-31x9-8IN/16864413682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 | You will need to be able to cut the shaft accurately into smaller sections.
 | 18 | 0.6 | 10.8 | 8mm ID x 16 OD x 5mm WD (f688z Flanged Bearings) | https://www.aliexpress.us/item/3256812035160016.html? | Flanged bearings used across the robot to house shafts.
 | 1 | 7.75 | 7.75 | Bungee Cord | https://www.revrobotics.com/rev-41-1163/ | Bungee cord keeping arm's lateral position in place.
 | 1 | 5.33 | 5.33 | Velcro | https://www.aliexpress.us/item/3256808114655678.html? | Velcro used to strap down battery in place.
 | 1 | 5.24 | 5.24 | Scotch Extreme Mounting Tape | https://www.amazon.com/Scotch-051141397252-Extremely-Mounting-414P-ST/dp/B018GKCI82/ | Mounting tape used to tape down wires and screwless electronics.
 | 1 | 2.89 | 2.89 | M2.5 washer | https://www.mcmaster.com/93475A196/ | Washer used in retaining a shaft.
 | 12 | 0.3158333333 | 3.79 | 10-32 washers | https://www.mcmaster.com/92141A011/ | Washers used in retaining shafts.
 | 1 | 1.48 | 1.48 | Electrical Tape | https://www.amazon.com/Duck-282289-Electrical-4-Inch-Single/dp/B007JSGNVQ/ | Electrical tape used in covering exposed wires.
 | 1 | 1.77 | 1.77 | Shrink Tubing | https://www.aliexpress.us/item/3256807959988149.html? | Shrink tubing used in covering exposed wires.
 | 1 | 5.05 | 5.05 | PTFE thrust bearing slider | https://www.mcmaster.com/2797T127/ | Must be identical to linked one.
 | 5 | 5 | 25 | Sets of M2, M2.5, M3, M4, 10-32 screws | https://www.aliexpress.us/item/2255799852960451.html? | (You can get a set of both rounded & socket head screws online or match the screws you buy by length, size, and amount to the CAD 1:1 by searching "screw" in the assembly and counting.)
 | 4 | 8.37 | 33.48 | 128-2Z Bearings | https://www.mcmaster.com/7804K115/ | Smaller-sized OD bearings used in housing shafts in gripper portion of MIST's arm.
TOOLS | 1 | 1 | 1 | 10-32 tap (for tapping shafts) | https://www.aliexpress.us/item/2255800936437301.html? | Tap used in tapping screw holes in the shaft type being used across MIST (4mm ID x 8mm OD)
 | 1 | 1 | 1 | 10-32 tap handle | https://www.aliexpress.us/item/3256807238346556.html? | Tap handle necessary to house tap being used.
 | 1 | 10.99 | 10.99 | Soldering Iron & Solder Kit | https://www.amazon.com/Soldering-Digital-Welding-Portable-Electric/dp/B08R3515SF/ | Soldering iron and solder necessary to connect electronics across MIST.
 | 1 | 6.77 | 6.77 | Wrench Set | https://www.aliexpress.us/item/3256806596445021.html? | Wrench set necessary to connect mechanical portions across MIST.
 | 1 | 15.09 | 15.09 | Allen Key Set | https://www.aliexpress.us/item/3256811924676788.html | Allen key set used to tighten and loosen screws in combination with the wrench set.
 | 1 | 20.41 | 20.41 | Wire Stripper, Cutter, and Crimper tool | https://www.aliexpress.us/item/3256809687963497.html? | Multifunctional electrical tool used for ensuring proper wire connections.
 |  |  | 760.22

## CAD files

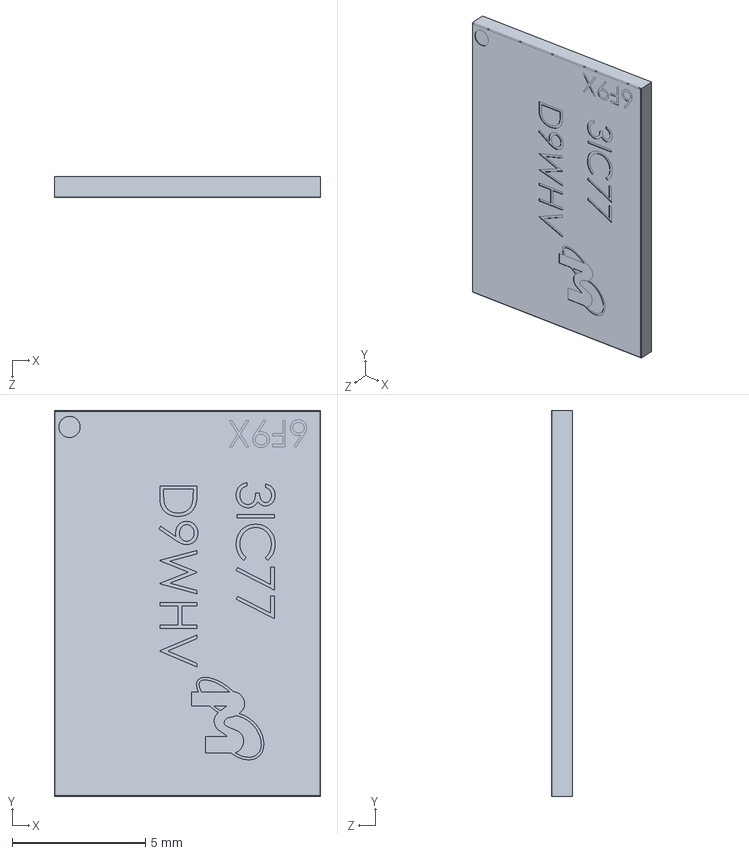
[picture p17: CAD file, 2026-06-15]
CAD/mist_creo/9FD77_D9WHV.SLDPRT
10.0 x 14.5 x 0.8 mm

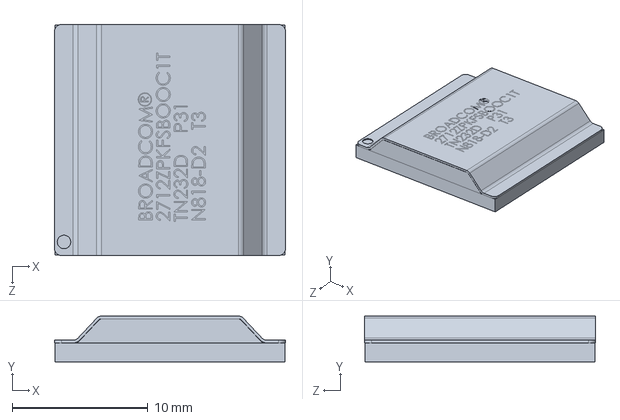
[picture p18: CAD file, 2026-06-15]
CAD/mist_creo/BROADCOM_1.SLDPRT
17.0 x 3.38 x 17.0 mm

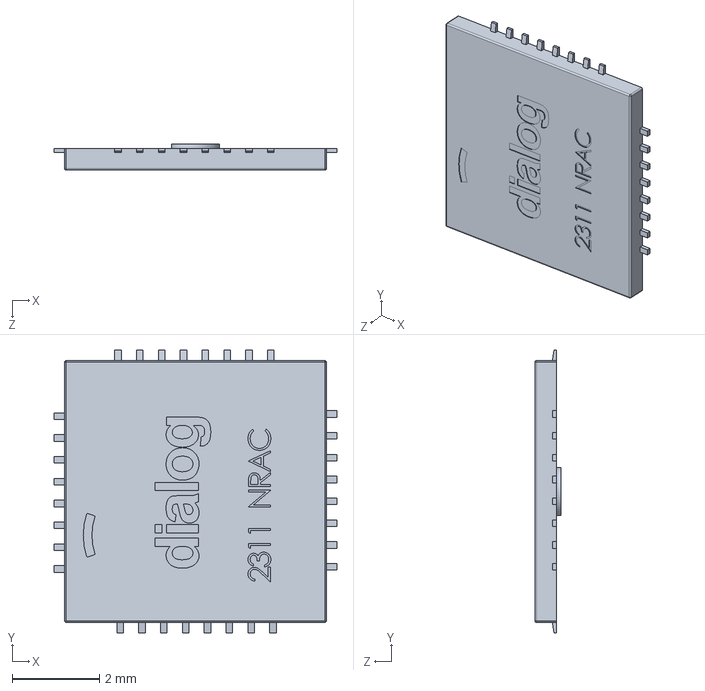
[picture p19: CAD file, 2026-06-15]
CAD/mist_creo/MxL.SLDPRT
6.48 x 6.48 x 0.6 mm

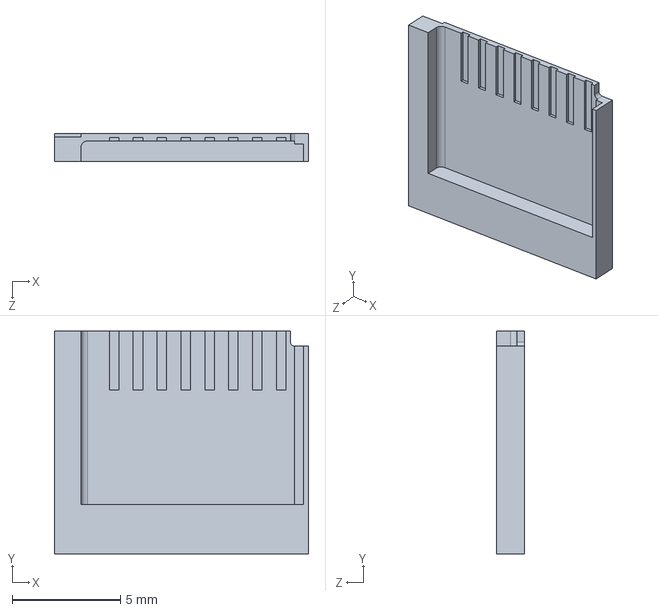
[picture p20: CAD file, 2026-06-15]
CAD/mist_creo/SD_CARD_V1.SLDPRT
11.7 x 10.3 x 1.30 mm

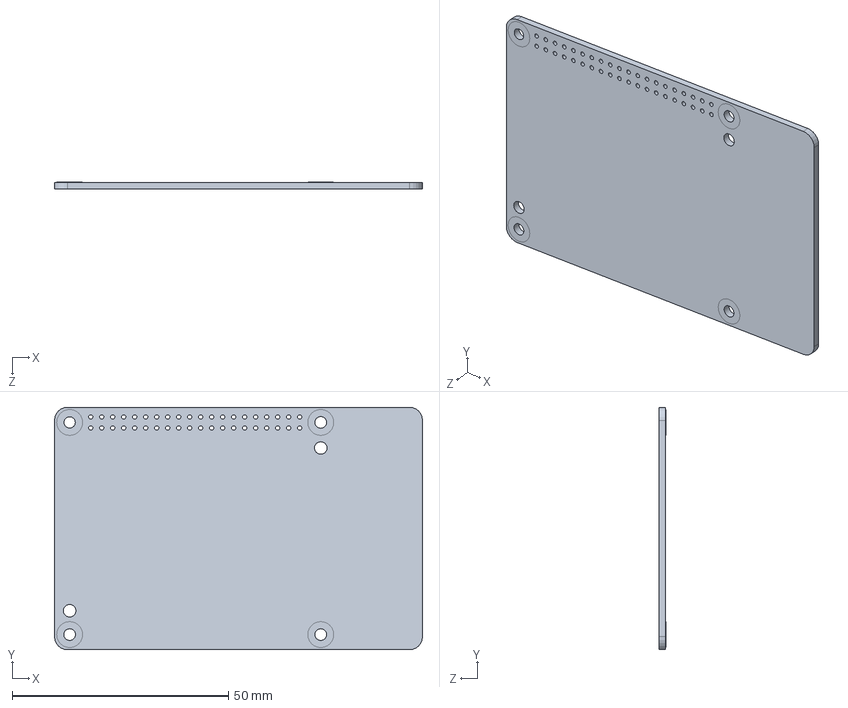
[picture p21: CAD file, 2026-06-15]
CAD/mist_creo/PLATE_RASPBERRY_PI_5.SLDPRT
85.0 x 56.0 x 1.70 mm

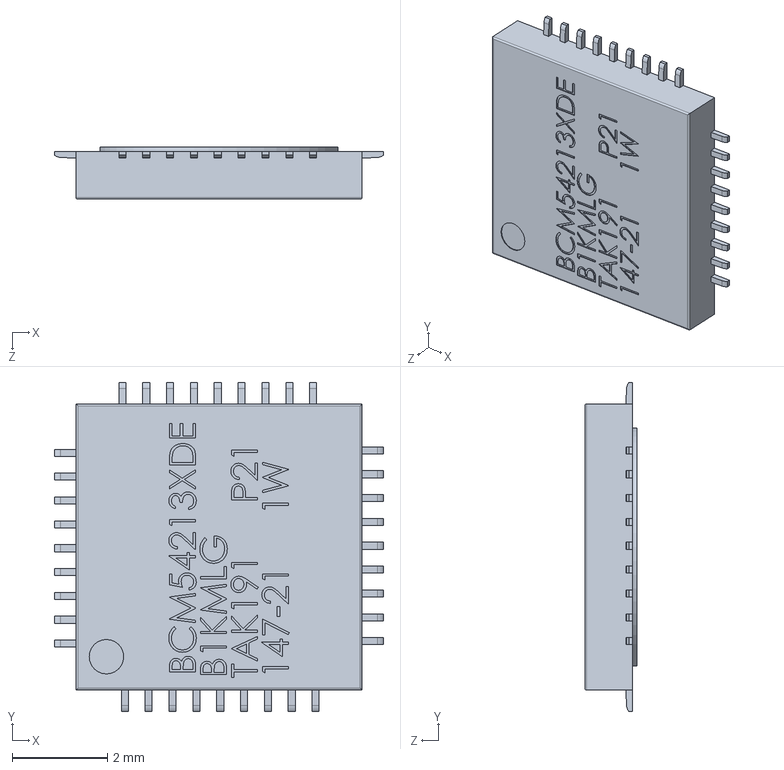
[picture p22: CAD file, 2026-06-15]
CAD/mist_creo/GIGABIT_ETHERNET_TRANSCEIVER.SLDPRT
6.90 x 6.90 x 1.10 mm

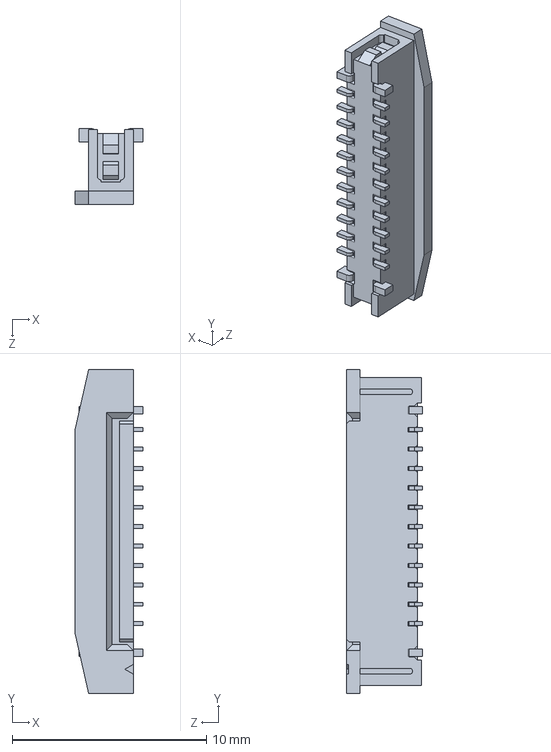
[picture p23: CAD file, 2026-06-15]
CAD/mist_creo/CAMERA_DISPLAY_2.SLDPRT
3.50 x 16.7 x 3.90 mm

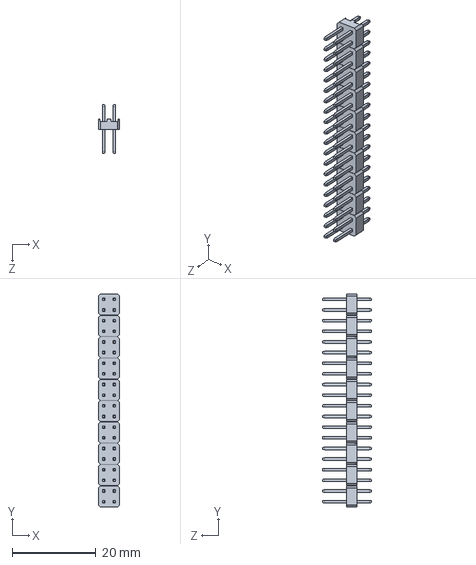
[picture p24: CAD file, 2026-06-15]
CAD/mist_creo/3.0_PIN_HEADER_10.SLDPRT
5.08 x 50.8 x 11.8 mm

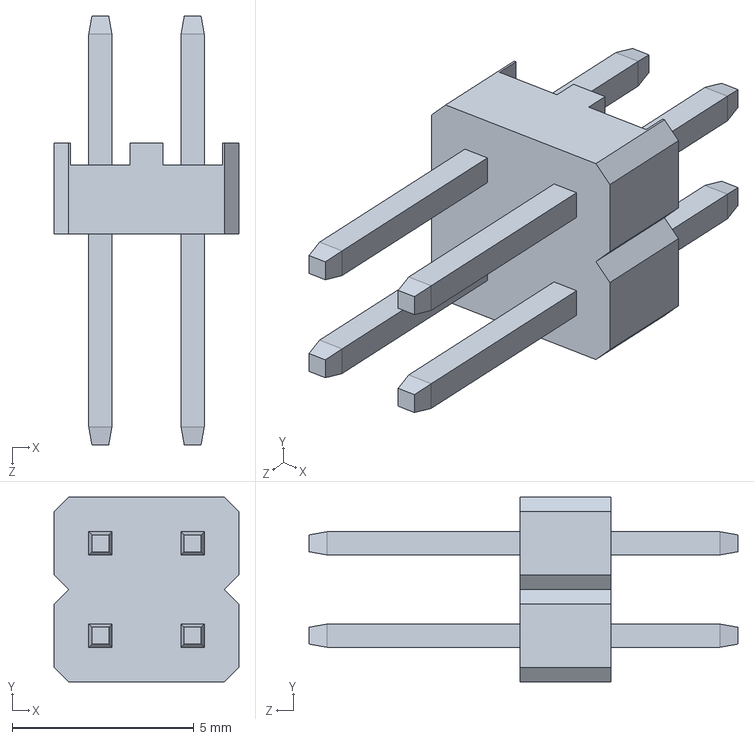
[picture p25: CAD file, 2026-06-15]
CAD/mist_creo/2.0_PIN_HEADER.SLDPRT
5.08 x 5.08 x 11.8 mm

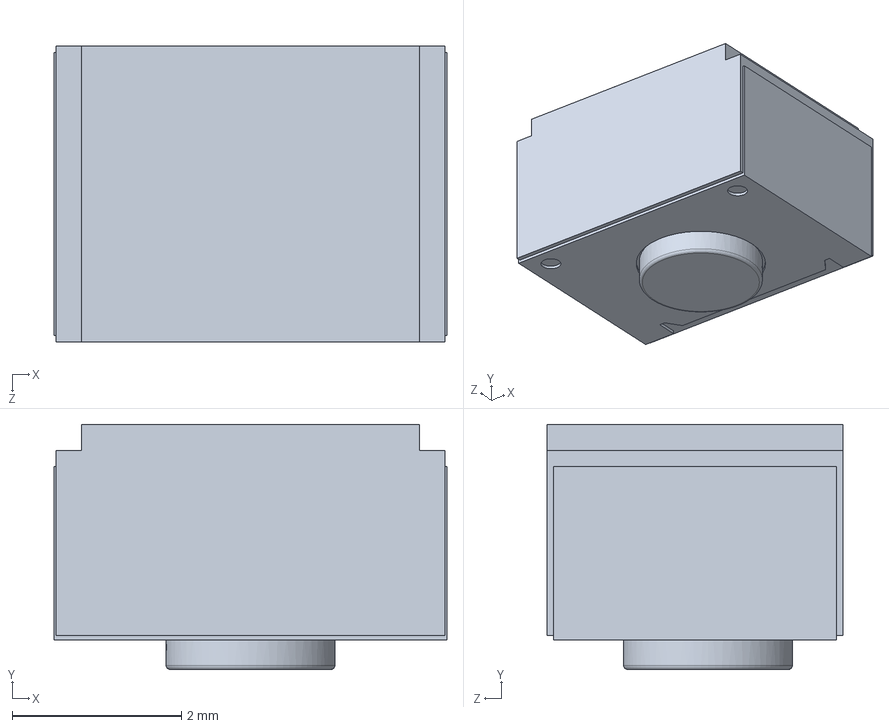
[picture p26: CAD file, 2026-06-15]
CAD/mist_creo/BUTTON_2.SLDPRT
4.65 x 2.90 x 3.50 mm

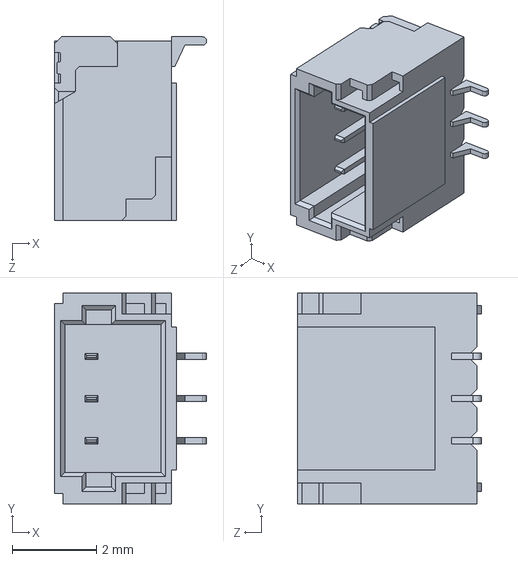
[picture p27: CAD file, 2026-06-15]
CAD/mist_creo/STOCK_2.SLDPRT
3.61 x 5.00 x 4.35 mm

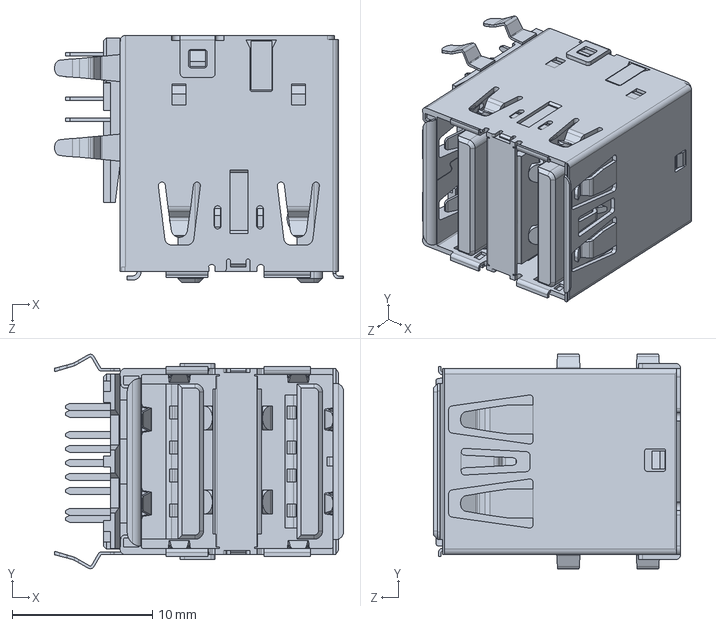
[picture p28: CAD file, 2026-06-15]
CAD/mist_creo/2xUSB_3.0_PORT.SLDPRT
20.6 x 15.3 x 17.7 mm

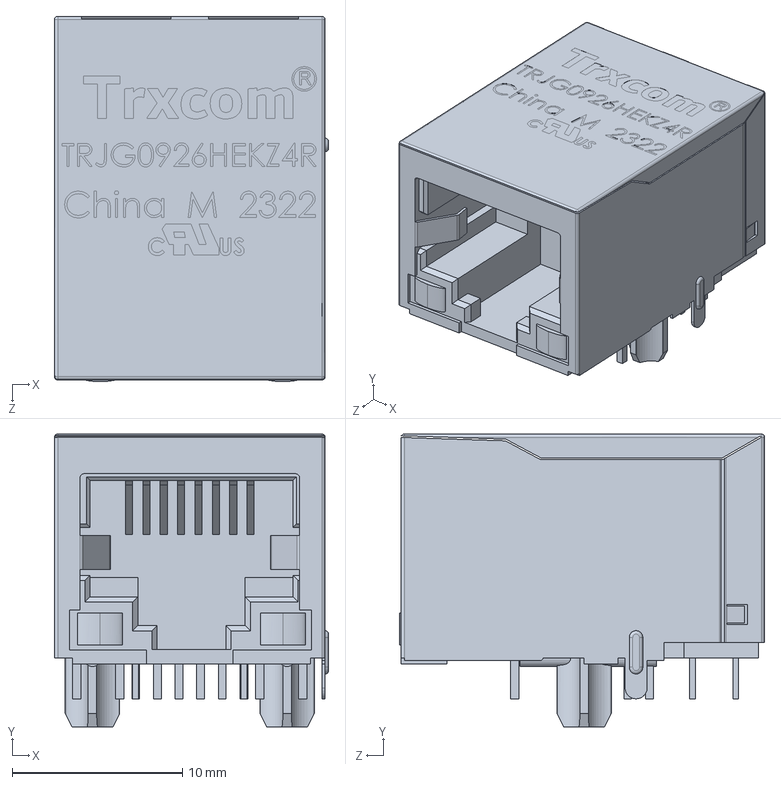
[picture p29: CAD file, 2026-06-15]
CAD/mist_creo/GIGABIT_ETHERNET_PORT.SLDPRT
16.1 x 17.2 x 21.4 mm

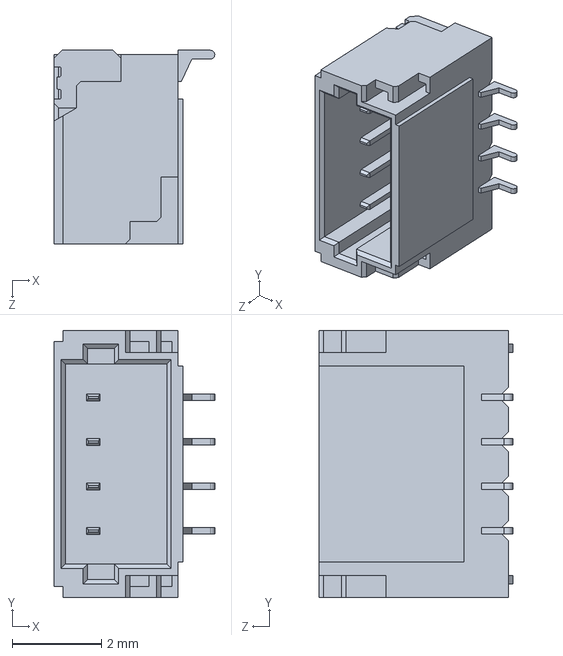
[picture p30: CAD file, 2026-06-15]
CAD/mist_creo/STOCK_1.SLDPRT
3.61 x 6.00 x 4.35 mm

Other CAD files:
CAD/mist_asm.stp
CAD/mist_creo/RASPBERRY_PI_5.SLDASM
CAD/mist_creo/SLOT_CARD_ASM.SLDASM
CAD/mist_creo/RP1_CO_CONTROLLER.SLDPRT
CAD/mist_creo/2xUSB_2.0_PORT.SLDPRT
CAD/mist_creo/BUTTON_MINI.SLDPRT
CAD/mist_creo/CAMERA_DISPLAY_1.SLDPRT
CAD/mist_creo/CARD_SLOT_METAL_PIN.SLDPRT
CAD/mist_creo/CONNECT_V1.SLDPRT
CAD/mist_creo/Case.SLDPRT
CAD/mist_creo/FEMALE_MICRO_HDMI_CONNECTOR.SLDPRT
CAD/mist_creo/FEMALE_USB_CONNECTOR.SLDPRT
CAD/mist_creo/METAL_PLATE..SLDPRT
CAD/mist_creo/Output Shaft.SLDPRT
CAD/mist_creo/PART3_V1.SLDPRT
CAD/mist_creo/PDM01.SLDPRT
CAD/mist_creo/Pan Head Cross Screw M1.6.SLDPRT
CAD/mist_creo/Pan Head Cross Screw M3.SLDPRT
CAD/mist_creo/Rubber Wire Cable Sleeve.SLDPRT
CAD/mist_creo/STOCK_3.SLDPRT
CAD/mist_creo/UBEC.SLDPRT

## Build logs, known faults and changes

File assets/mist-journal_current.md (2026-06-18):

# MIST — Journal Export

- Exported at: 2026-06-18T22:07:09Z
- Project ID: 2463
- Entries: 83

## Entry 1
- ID: 3694
- Author: Esia
- Created At: 2026-04-24T10:45:09Z

### Content

We've begun working on laying out the materials needed (motors, electrical components, physical framing) to make MIST (the rice cooker robot lol) a reality, as well as starting on the CAD of the robot's base whilst planning on eventually developing semi-humanoid legs to add onto the base and a functional lid mechanism to emulate an actual rice cooker.

Screenshot 2026-04-24 034224.png

### Recording Links

- https://lookout.hackclub.com/api/media/73c03f60-d6fb-4926-9cfd-aa727cfd0269/video.mp4
- https://lookout.hackclub.com/api/media/e32ee504-f344-4883-b765-bb6c7ec15c7f/video.mp4

## Entry 2
- ID: 3721
- Author: Umarbek
- Created At: 2026-04-24T15:03:42Z

### Content

In planning creation of MIST with Esia earlier today, we've planned a complicated system for the robot, with a lot of resource intensive elements such as face-recognition, object-detection and autonomous navigation and balancing. 

Here, I've tested the possibility of using DietPiOS on the raspberry pi as it doesn't have GUI, relying solely on terminal. However, we will have to animate eyes for the robot on a screen, and the choices we had were either to use ASCII art (we'll definitely add this if we have extra time) or render from zero using lower-level programming language (golang was chosen in this scenario as it will most likely be the singleton which will control the entire robot mechanics later on due to its speed and concurrency and all).

The result of this was simple animated (bouncing left and right) eyes for the screen. I couldn't figure out how to make it automatically detect the screen size due to complexities with low-level kernel architecture so I hard-coded whatever looked right to me for now 😅. Now that the idea works, I will next continue on defining the function loop for the robot and then continue with designing all the eyes states & implementing them in golang.

Final Eyes moving:
Screenshot 2026-04-24 at 22.44.31.png

Original Glorious Cube that worked, bringing hope in this idea:


### Recording Links

- https://lookout.hackclub.com/api/media/026a0bd4-ef73-40e5-b696-359a6614e63e/video.mp4
- https://lookout.hackclub.com/api/media/16481bfa-b237-43ed-a15b-0fd930c1bbcb/video.mp4

## Entry 3
- ID: 3986
- Author: Umarbek
- Created At: 2026-04-26T03:25:57Z

### Content

Following yesterday's success of running animated eyes in DietPi, operating system without graphical operating system, today I've updated my setup to run on MacOS. Now it automatically compiles to the correct operating system depending on the host, creating a window for Mac and wiring to the frame buffer on Linux. Here's the new (now blue) ping-pong eyes running on Mac:

(I know it might look intimidating but next thing I'll do is ensure correct colours and start implementing all the eye & mouth variations, making it more accurate to the source.)

I've also researched on all the possible faces for MIST, categorising all the various the ones I found into few categories by introducing parameters such as line-width, corner-radius, size, and rotation. 



### Recording Links

- https://lookout.hackclub.com/api/media/5870a76a-7e8f-4c3b-add2-98061efec9b3/video.mp4

## Entry 4
- ID: 4160
- Author: Umarbek
- Created At: 2026-04-27T02:33:07Z

### Content

I have continued the process of classifying the face types and figured out a way how to further break down each eye and mouth into basic shapes, allowing me to implement the least amount of facial features while achieving as much as possible. Next, I will start implementing them.



### Recording Links

- https://lookout.hackclub.com/api/media/683e05c7-87ec-437c-8347-b03e6e2e362e/video.mp4

## Entry 5
- ID: 4177
- Author: Umarbek
- Created At: 2026-04-27T04:38:06Z

### Content

I have finally implemented some of the faces and figured out a way how to animate them. While it functions, each change is still hand-written and further steps for this would be to finish implementing all the possible facial features, create a framework to properly animate them in a simpler way (maybe using an http server or something on those lines) and creating pre-configured animations such as "default-state", "curious", "loading", "charging", "text", and more. Here are some of the faces we got so far:



### Recording Links

- https://lookout.hackclub.com/api/media/a6880284-f1fe-44db-858e-74e1314de928/video.mp4

## Entry 6
- ID: 4294
- Author: Umarbek
- Created At: 2026-04-28T01:57:43Z

### Content

We've successfully prooved connected PS5 controller to both Mac and RaspberryPi, allowing us to rely on it as means of control in future for our robot. We've written proof of concept code to get the data from the controller, which includes every button press/release and movement of joysticks. Next stage for this would be to decide on how we want MIST to be controlled and implement as planned. (It functions on both MacOS and Raspberry Pi!)



### Recording Links

- https://lookout.hackclub.com/api/media/93c8a870-bbe5-4fd5-aa43-449a9fa7a26a/video.mp4
- https://lookout.hackclub.com/api/media/3302e526-94e0-4ada-bf5a-e6cae6ba62f2/video.mp4

## Entry 7
- ID: 4460
- Author: Umarbek
- Created At: 2026-04-29T07:39:54Z

### Content

In this session, I've analysed Disney's approaches in their Droid and attempted to write a pseudo-code algorithm for our robot. While it isn't finished, now there are some ideas on how movement and control should be handled and it is more clear on how to continue.


### Recording Links

- https://lookout.hackclub.com/api/media/3e3b9fc0-bfd3-4016-b8ca-d296ae6b9f8a/video.mp4

## Entry 8
- ID: 4462
- Author: Umarbek
- Created At: 2026-04-29T08:44:30Z

### Content

With Esia, we've caught up on the progress. He've shared on the parts he've selected for the robot and we've reviewed the motor options, approximating battery life, power, and more.



### Recording Links

- https://lookout.hackclub.com/api/media/aa841e17-7862-493c-bfeb-3292589eeeff/video.mp4

## Entry 9
- ID: 4624
- Author: Umarbek
- Created At: 2026-04-30T14:07:58Z

### Content

Today I've fixed some bugs on the facial software and finished implement all the eye/mouth types. I've also expanded upon what can be animated. The next step would be to clean up the codebase and figure out final way to let the higher-level brain to control the states of the face. (The demo is now animated)



### Recording Links

- https://lookout.hackclub.com/api/media/5c981180-3157-4423-be4e-4dcb309924af/video.mp4

## Entry 10
- ID: 4649
- Author: Esia
- Created At: 2026-04-30T17:57:49Z

### Content

Umarbek and I have now figured out the core of the electronics system together and I've continued CADDING whilst having a better vision of what the project will end up looking like.

A brief list of the electronics we'll be using:

12 servos and 4 DC motors 
A 3 cell LIPO battery.
A motor distribution board (PCA9685 - Adafruit)
Custom motor controller PCBs for the DC motors
Raspberry Pi5 (sourcing it ourselves) as the computer
A power bank for the Pi5
A PS5 controller (sourcing it ourselves probably)
12v to 6v DC converter for the servos
voltage sensor module to read battery life

Screenshot 2026-04-30 10.55.50 AM.png

### Recording Links

- https://lookout.hackclub.com/api/media/7813575c-b4e9-4d54-8d99-accfd3d6d907/video.mp4
- https://lookout.hackclub.com/api/media/8d835758-2ae4-44bc-bafb-96150c5e8d85/video.mp4

## Entry 11
- ID: 4730
- Author: Umarbek
- Created At: 2026-05-01T08:10:48Z

### Content

The hardest challenge for me is to create a behaviour that makes the robot feel real/alive. Therefore, I've written more on how should the robot's decisions/actions/movements be handled, coming up with what seems like an elegant "filtering" solution to its actions, and hierarchy of movements.


### Recording Links

- https://lookout.hackclub.com/api/media/f5a1cfda-4ccd-4e5a-9609-e60a23b87ef4/video.mp4

## Entry 12
- ID: 4829
- Author: Esia
- Created At: 2026-05-01T23:26:35Z

### Content

I've completed the CAD for one leg segment out of a total six that I will need to CAD. We've decided on using a belt drive beginning inside the robot's base and ending at the wheels, accelerating them.

We'll be using GT2 belts as they are the cheapest option available and using 0.375" hex shafts everywhere we decide to place an axle of rotation. 

Here's a front view of what the inside of one leg segment looks like:

Screenshot 2026-05-01 053201.png

### Recording Links

- https://lookout.hackclub.com/api/media/8c873caa-98bf-4587-99f5-c955e238557a/video.mp4

## Entry 13
- ID: 4852
- Author: Umarbek
- Created At: 2026-05-02T03:21:42Z

### Content

I've explored upon the emotional models of human mind and wrote a little of pseudo-code to plan out how MIST will function. Additionally, together with Esia, we've thought of how autonomous-following functionality could work, and attempted running whisper locally for Speech to Text, and checked if Gemini would be a good "brain" for the MIST (it turned out to be surprisingly good, I now understand why Google wants to just put their models on robots)

Screenshot 2026-05-02 at 12.18.46.png

### Recording Links

- https://lookout.hackclub.com/api/media/6a2de2ed-2a25-4845-b4c1-bda2144b6f36/video.mp4

## Entry 14
- ID: 5227
- Author: Umarbek
- Created At: 2026-05-03T05:03:03Z

### Content

We've decided that we'll add a camera to MIST, which will inference OpenCV or some other object detection algorithm as well as facial recognition. I've successfully set up OpenCV face detection, ready to be integrated to the main singleton function. I must, however, still optimise the code and figure out a more elegant approach to object and facial recognition.

Screenshot 2026-05-03 at 14.02.08.png

### Recording Links

- https://lookout.hackclub.com/api/media/c4f07891-65a2-4095-a853-8836b233251a/video.mp4

## Entry 15
- ID: 5410
- Author: Umarbek
- Created At: 2026-05-04T10:07:50Z

### Content

Further developed the idea of emotional vector and mapped out which emotions lead to what changes in faces. Finally have a functioning face with a fancy boot animation. Next I'll start working on coding for the servos and figuring out how to simulate cushioning.



### Recording Links

- https://lookout.hackclub.com/api/media/d23e75e9-98e4-41c1-bcaa-438a7c2405cd/video.mp4

## Entry 16
- ID: 5580
- Author: Umarbek
- Created At: 2026-05-05T10:45:16Z

### Content

I've run Yolo11n object detection model using python instead of go, which resulted in a higher accuracy and quantity of objects detected. However, it was still very low as we were only getting "person", "smartphone", "fridge" for any object I've tried. Object detection seems to be a sub-optimal method for eyes of our robot. 

Next, I've tested usage of Gemma models for the robot, and they blew all my expectations. After such an experience, you start understanding why Google just puts Gemini into all of their robots and why competitors follow–it's just disgustingly simple while performing better than any other method available. Trying various sizes ranging from Gemma3:270m to Gemma4:31b, the latter one provided sufficient intelligence to comfortably operate a prompt+picture simulated robot, bringing hopes in its autonomy. While this goes against original idea of full offline robot controlled with raspberry pi 5, it brings the end goal of intelligent robot to the line.

Next, I will look at how other robots or AI-apps create harness and how could our one look like for MIST to integrate Gemma while keeping it 'alive'.



### Recording Links

- https://lookout.hackclub.com/api/media/32385c7d-ebe9-4f3e-9a0c-dcfdfa072252/video.mp4

## Entry 17
- ID: 5700
- Author: Umarbek
- Created At: 2026-05-06T07:36:59Z

### Content

We've encountered some issues with motors, which after some discussion were solved. I've quickly tested smaller models for the brain, made a brief map of the current code repository for presentation to the team this weekend.



### Recording Links

- https://lookout.hackclub.com/api/media/1720a2b1-344a-4b0e-8d7f-aae7b555a3d2/video.mp4

## Entry 18
- ID: 5869
- Author: Umarbek
- Created At: 2026-05-07T09:52:28Z

### Content

I've tested few more smaller AI models, successfully connected to local instance of Ollama through golang and implemented particular AI functionality. 

Picked a camera for the robot and more...
Screenshot 2026-05-07 at 18.52.16.png

### Recording Links

- https://lookout.hackclub.com/api/media/acbfd201-6021-4357-a483-f68888b5722e/video.mp4

## Entry 19
- ID: 6044
- Author: Esia
- Created At: 2026-05-08T06:15:08Z

### Content

I spent a significant portion of time iterating through joint designs to manage actuating each leg's rotation separately. Originally, I went into pushing myself to try to create an impossibly compact design to remain accurate to the show all the while in our miniature formfactor.

Eventually I had to compromise and choose functionality over accuracy but after receiving second opinions from Umarbek, William, and outside sources, I determined this would be the best way to approach the problem and so I began working on a modular joint that we can use across the entire robot.

Screenshot 2026-05-07 231436.png

### Recording Links

- https://lookout.hackclub.com/api/media/7d2b6ae1-12c9-4942-9c66-09ea27bdfc14/video.mp4
- https://lookout.hackclub.com/api/media/e2a33ce6-6770-4ac2-82e1-5c67b1775964/video.mp4
- https://lookout.hackclub.com/api/media/b828f226-6e9d-4ea1-919d-cc6e571f1d0c/video.mp4

## Entry 20
- ID: 6098
- Author: Umarbek
- Created At: 2026-05-08T15:13:21Z

### Content

I have written the logic for the camera module, which works on Mac and (should) work on MIST as well. We'll test it on the robot during her assembly.

I understand why they do so. This techniques works too well to ignore it or invent drastically something new. An interesting observation from their [blog](https://deepmind.google/blog/gemini-robotics-er-1-6/) is that the core fundamental idea behind this model is its ability to identify objects, their center-points, and boxes. This information is then used in a standard way by LLM creating a script to calculate the distances/relationship between dots/boxes to then decide on what to do. 



### Recording Links

- https://lookout.hackclub.com/api/media/67de4cb7-f098-4924-8d4a-205e41f94336/video.mp4

## Entry 21
- ID: 6215
- Author: Esia
- Created At: 2026-05-09T06:33:20Z

### Content

I continued to work on revamping the joint into becoming modular and usable across the entire robot. I essentially finished it, and I've left to work on integrating it where needed in the robot.

The joint's design relies heavily on coaxial features to manage stability and mounting. There are a couple mounted bearings for stability purposes and one on either side to mount each leg directly onto.

Screenshot 2026-05-07 230949.png
Screenshot 2026-05-08 223710.png

### Recording Links

- https://lookout.hackclub.com/api/media/70515fef-0fa0-42f9-a5ac-2fa92412ee17/video.mp4
- https://lookout.hackclub.com/api/media/89d895ee-1b3a-4481-94d4-5ff8573f50a8/video.mp4

## Entry 22
- ID: 6716
- Author: Esia
- Created At: 2026-05-12T05:01:50Z

### Content

I finished the first two leg segments of MIST entirely, and began to work on the third leg segment before I realized how impractical the design overall was and succumbed to dissatisfaction.

Screenshot 2026-05-09 035626.png

So, I thought to myself why am I making such a CHUNKY joint in the first place? Of which, I deduced two main reasons along with a bad design choice I had made previously.

These two reasons being:
1. I was designing too much for stability's sake, using dead axles and bearing combos wherever I could to support the robot's weight on all sides of the legs.
2. I was insistent on the fact that a motor could not possibly fit within the leg's volume and that a belt drive originating from MIST's body would be necessary.

For the first reason, I now say: it'll be fineeee...
In response to the second reason, I now say: small motors exist, don't be so stubborn and find one that'll work. (ehem: 



The bad design decision I made being: I placed the servo in a vertical position, independent of any leg segment, rather than storing it within the former leg segment of each rotational piece. Such a setup took up too much space and led to intersecting conflicts.

So, with a new resolve and an even BETTER (and simpler) design in mind, I now embarked on the journey toward redesigning the joints for a third time.

### Recording Links

- https://lookout.hackclub.com/api/media/90f5964f-3105-4445-8038-a84a89962956/video.mp4
- https://lookout.hackclub.com/api/media/2b33c7e6-fea8-4aab-8c45-d09612915324/video.mp4
- https://lookout.hackclub.com/api/media/5247c1c3-9c12-434f-8bd1-3f1582cd37f0/video.mp4
- https://lookout.hackclub.com/api/media/019000b2-f068-4050-8a70-c0c3383134dc/video.mp4

## Entry 23
- ID: 6772
- Author: Umarbek
- Created At: 2026-05-12T14:03:02Z

### Content

Since I've implemented all the eye and mouth types at the beginning, now with all the screen transformations, some of them having changed significantly to the point I must rewrite the logic behind their rendering, thus here it is more time to drawing MIST's face :sob:



### Recording Links

- https://lookout.hackclub.com/api/media/71add299-3c4f-4b92-8f96-fe99e061460d/video.mp4

## Entry 24
- ID: 6773
- Author: Umarbek
- Created At: 2026-05-12T14:03:38Z

### Content

Mujoco's interface while intimidating at first, is growing on me. I've been learning their XML formatting and simulation logic; while we wanted to import the CAD models from CREO to Mujoco right away, I've learned that it is too much, and we should rather aim to recreate a simplified copy of MIST, where only moving parts matter, and focus is rather on weight distribution, moment of inertia and other physical parameters rather than assembly. Thus, here I am, manually typing into XML to see if it works at all



### Recording Links

- https://lookout.hackclub.com/api/media/e31cea6b-1676-4520-a262-2d67383b6250/video.mp4

## Entry 25
- ID: 6781
- Author: Umarbek
- Created At: 2026-05-12T15:16:22Z

### Content

Nothing too revolutionary, just iterated over all the eyes and fixed them one by one–finally made the non-pixelated versions of fancy-eyes (character eyes); below you can see the one with X's. Next, I will work on mouths. 

I also developed way cleaner approach of animating the eyes, greatly reducing the complexity in the main controller. Now it only requires this: 

```
package main

import (
	"mist-os/screen"
)

func main() {
	sc := screen.NewScreen(800, 480)
	if sc == nil {
		return
	}
	defer sc.Close()
	testFaces(sc)

	sc.StartLoading(0, 0.5)
	sc.SetFace("fancy-x", "none")
	sc.Run()
}
```



### Recording Links

- https://lookout.hackclub.com/api/media/1637479e-8703-4b37-9683-d3b7a0701c18/video.mp4

## Entry 26
- ID: 6866
- Author: Umarbek
- Created At: 2026-05-13T02:35:29Z

### Content

Addition to my previous journal: I was able to animate in Mujoco, now I am trying to figure out on how to simulate it. Here, you can see an animation of a cube rotating:

Screenshot 2026-05-13 at 11.32.54.png

### Recording Links

- https://lookout.hackclub.com/api/media/e727a20c-720b-4e75-855e-f45028ae6761/video.mp4

## Entry 27
- ID: 7247
- Author: Umarbek
- Created At: 2026-05-15T12:44:39Z

### Content

I've been looking through the current schema for electronics, understanding how to connect to each component and checking for alternatives.



### Recording Links

- https://lookout.hackclub.com/api/media/e812e053-596b-400d-94f4-4ea94474e825/video.mp4

## Entry 28
- ID: 7253
- Author: Umarbek
- Created At: 2026-05-15T13:51:28Z

### Content

I've continued the auditing of the components, and weighted the choice between bluetooth controllers such as ones of consoles and FPV-styled radio-controllers.

Then, I've written pseudo-code for self-positioning and ground angle approximation for a robot whose base is variably tilted. 

There are many many degrees of freedom. I've mapped some possible movements to a controller for now. (still unfinished)



### Recording Links

- https://lookout.hackclub.com/api/media/8fb666bd-ad79-4d44-b459-3b3fb31a7595/video.mp4

## Entry 29
- ID: 7379
- Author: Umarbek
- Created At: 2026-05-16T07:41:39Z

### Content

Expanded upon yesterday's work on figuring out robot's movement controls. I've mapped our controller's inputs to SDL, and attempted assigning them the correct motors for our robot. It is a challenge, as there are so many degrees of freedom in MIST, but doing this, it is now way clearer on how the code for motors should look like.



### Recording Links

- https://lookout.hackclub.com/api/media/739c8c01-57ae-49ed-a001-2444ed00942a/video.mp4

## Entry 30
- ID: 7740
- Author: Umarbek
- Created At: 2026-05-18T04:42:34Z

### Content

I've been working on Mujoco simulations, experimenting with the XML files and trying to find a way to properly see what I'm typing without having to run a python simulation and export it as a video every time...
Screenshot 2026-05-18 at 13.41.41.png

### Recording Links

- https://lookout.hackclub.com/api/media/bedeef45-fcb5-4023-8220-34a03268dba7/video.mp4
- https://lookout.hackclub.com/api/media/97053490-86f1-434e-9b40-7756d39ffbb4/video.mp4

## Entry 31
- ID: 7741
- Author: Umarbek
- Created At: 2026-05-18T04:46:18Z

### Content

I've learned of existence of visual studio code Mujoco viewer extension, which turned out to be a game-changer! It allowed to simulate the model in real time and gave an already set up beautiful environment with good lightning. Next, I'll be figuring out how to control the digital robot with external feedback during simulation. 

Btw, this model is whatever I could scramble by myself and isn't the model being used for CAD or the model we'll actually simulate later, it is purely for testing purposes.

Screenshot 2026-05-16 at 22.53.01.png

### Recording Links

- https://lookout.hackclub.com/api/media/4c3ea4c0-9171-4803-a020-533e36372e9a/video.mp4

## Entry 32
- ID: 7898
- Author: Umarbek
- Created At: 2026-05-19T03:36:02Z

### Content

In this session, together with Esia, we've been revising and evaluating the choices of motors and their positioning. Several different approaches were discussed and we've come at more elegant design which will (hopefully) help simplify building of front legs, bringing it closer to original design.



### Recording Links

- https://lookout.hackclub.com/api/media/1b6a3850-e437-45c6-9e6d-fcdefe390879/video.mp4

## Entry 33
- ID: 9258
- Author: Umarbek
- Created At: 2026-05-26T02:59:59Z

### Content

Before writing Gobot code, I've realised I must know which pints must I connect to in order get data and control the actuators. This marked the beginning of series of great circuitry sessions which consists of a continuous loop of me searching for non-existent documentation of electrical components, getting humbled by power distribution calculations in order to avoid frying the precious raspberry pi, and (hopefully) correctly wiring the components.

Screenshot 2026-05-26 at 11.56.27.png

### Recording Links

- https://lookout.hackclub.com/api/media/70f7bbd9-917b-4036-aa4c-962078268ec3/video.mp4

## Entry 34
- ID: 9260
- Author: Umarbek
- Created At: 2026-05-26T03:03:34Z

### Content

Continuation of the previous session, where I've been working on circuitry for MIST. This time, I've only concentrated on wiring, putting Gobot and programming aside (I'll come back to it once the wiring will be completed.) All that's left is the hardest parts of this process—wiring 8 servos and 4 motors, figuring out how to distribute power across all of these things without having to get dozen separate batteries.

Screenshot 2026-05-26 at 11.56.39.png

### Recording Links

- https://lookout.hackclub.com/api/media/d1a65c28-dd19-4d14-9f14-397c3b01358b/video.mp4

## Entry 35
- ID: 9262
- Author: Umarbek
- Created At: 2026-05-26T03:05:46Z

### Content

Continuing from the previous session, I've finally finished connecting the servos! All that's left is power, motors, and peripherals (they'll just connect through USB's so it won't be as much of hurdle as actual circuitry components.)



### Recording Links

- https://lookout.hackclub.com/api/media/b056a568-a73e-42de-a9a5-8292f88df3ba/video.mp4

## Entry 36
- ID: 9298
- Author: Umarbek
- Created At: 2026-05-26T05:55:11Z

### Content

Understood how wiring and controlling of brushless motors work, yet now there are questions whether it will be strong enough for our heavy robot. Will continue later on it.



### Recording Links

- https://lookout.hackclub.com/api/media/f6620127-5ee7-4e61-97a9-5f0446cfd1da/video.mp4

## Entry 37
- ID: 10080
- Author: Umarbek
- Created At: 2026-05-29T06:49:53Z

### Content

Until now, I've been creating separate modules for each part of the robot: camera, AI, screen, imu, and more. After reading an article on how all these parts are combined in robotics, I've created a basic diagram for the data flow between different packages. I've been trying to figure out how to actually move the robot (which turns out is a part of Control theory), that I've been studying after this session at my own time.

Screenshot 2026-05-29 at 15.47.00.png

### Recording Links

- https://lookout.hackclub.com/api/media/234dcb60-f5c7-443d-b1ae-30f7e6c7564f/video.mp4

## Entry 38
- ID: 10092
- Author: Esia
- Created At: 2026-05-29T09:23:55Z

### Content

I began working on the 3rd version of the joint around this time. In this new version of the joint, there's a few differences:

1. The servo is mounted directly to the joint itself and the leg that precedes it. This is just a better way of coupling rotational motion rather than what I was doing before where the servo was connected only to itself.




2. The motor is a smaller alternative that can be mounted directly in the leg. This removes the need for a chain of belts connecting the chunky mini cim motor we were previously using:



Thus making our joints more compact overall.

3. There is simply less things to mount overall, so axial stability is less of a concern. This lets us use just one bearing for support rather than the bearing stack that was being used before.



### Recording Links

- https://lookout.hackclub.com/api/media/2cde9235-83ac-4cb1-a8d2-085cfc29ac14/video.mp4
- https://lookout.hackclub.com/api/media/9706a848-2cf6-469c-b5f4-1f129247040a/video.mp4

## Entry 39
- ID: 10098
- Author: Esia
- Created At: 2026-05-29T09:48:47Z

### Content

With the 3rd version of the joint done, I returned back to finishing the design of the legs. This part was rather simple, I just finished the shells of each leg segment that remained for the robot and attached a joint to each respectively. This allowed us to go from this:



To this:



And by shell, I mean literally that. These leg segments are just hollow and empty, only existing so that our project remains loyal to the show we are deriving it from.




With an entire leg done, I mounted it onto the robot, did some mirroring magic to receive the model of the second version of this leg we'll be using and voila: 

Screenshot 2026-05-29 023823.png
Screenshot 2026-05-29 023823.png
Screenshot 2026-05-29 023752.png

### Recording Links

- https://lookout.hackclub.com/api/media/4dee5033-5493-44d3-8d79-0c1e83e73d37/video.mp4
- https://lookout.hackclub.com/api/media/99fadd5c-3786-4258-b535-f6de5c78851d/video.mp4

## Entry 40
- ID: 10099
- Author: Esia
- Created At: 2026-05-29T10:04:48Z

### Content

I basically took some time to further develop the wiring of our robot and make sure everything checks out:



It was rather informal and I just did it on the figma board with marker and no pin layouts, but I just established a baseline for Umarbek to eventually build upon with specific pin connections and more detail.

Afterwards Umarbek left some comments which you can see on the sticky notes.

At the same time, I also very minimally began on the cad for the other 2 legs remaining on the robot (being the skinny legs).

### Recording Links

- https://lookout.hackclub.com/api/media/e37accac-9d07-4eaf-8377-e5b673488e2b/video.mp4

## Entry 41
- ID: 10108
- Author: Esia
- Created At: 2026-05-29T10:56:27Z

### Content

So I 3D printed some of the stuff, including the cover for the servo horns which our robot's joints use.. take a look at it:



Issue. The holes are incredibly small. Now, I have never seen screws that small other than in the assembly of extremely delicate electronics. In our case the weight of a robot leg is resting upon those screws.

Screws in general tend to be stronger than needed for all purposes I've been exposed to, so to follow that trend I chose to also upsize our screws as well, mostly for the peace of mind. In order to do so, I'd have needed to design a custom servo horn and ensure it can actually fit onto the tooth profile of a servo.

So I did some research on previous attempts:

Screenshot 2026-05-29 033022.png
Screenshot 2026-05-29 033100.png

Printed a few variations with different tooth profiles for mounting:



And had some moderate success with fit at the very least.



What I found is that generally 3D printers tend to struggle with printing details finer than the nozzle size (in my case 0.4 mm):



Even the slicer sometimes turns the details into goop:



So you have to work around that. I did so by just undersizing the tooth profile (scaling it down by 2%) and relying on a press fit.

I also started working on doing some math on what drive ratios I'd need to accelerate with maximum efficiency. It involved a significant chunk of research and honestly most of it was just physics. Here are some of the constants I defined before getting into the math:



### Recording Links

- https://lookout.hackclub.com/api/media/20d9913f-4804-4faa-8477-c5a1e76b8ce0/video.mp4

## Entry 42
- ID: 10116
- Author: Esia
- Created At: 2026-05-29T11:28:12Z

### Content

To decide the drive gear ratio we'd be using for our wheels, I had to do the math with the constants I had given myself.



I basically calculated the maximum force the ground could theoretically exert against our wheels before they started slipping and decided that it would only make sense to go up to that fast and geared such that we could go at that speed within our motors' efficient range of operation (~80%)

The reason we decided it was necessary to be capable of going so fast (18.14 m/s) is because of this clip from Pantheon: [https://youtu.be/1tU2ZMSHPR4?t=954](url)

We want to stay accurate to the show, and sometimes it posed challenges like having to push your robot to go _theoretically_ as fast as a car on a road.

And with the gear/pulley ratio now calculated, I modified the model to match it appropriately:



### Recording Links

- https://lookout.hackclub.com/api/media/318c4d66-f633-489e-8f08-5504fa8e8c16/video.mp4

## Entry 43
- ID: 10343
- Author: Umarbek
- Created At: 2026-05-30T08:05:08Z

### Content

With the Burnout pitch deadline approaching, I've started documenting our total progress on MIST in a singular document. In writing it all into document, I've realised how far we've come. While I've written most of the pitch, it is still to be completed.

Screenshot 2026-05-30 at 16.55.33.png

### Recording Links

- https://lookout.hackclub.com/api/media/d79effb6-2c98-4544-8783-e790e19756d2/video.mp4

## Entry 44
- ID: 10344
- Author: Umarbek
- Created At: 2026-05-30T08:07:11Z

### Content

Continuation from previous time, I've read through other people's failed and successful burnout pitches, styling ours in a similar manner to ensure we'll pass it. I've completed all I could, leaving some space for my teammate to fill out (parts specific to his knowledge and skill that I don't know how to answer.) We're planning to submit it by Saturday evening.

Screenshot 2026-05-30 at 17.06.09.png

### Recording Links

- https://lookout.hackclub.com/api/media/afc3c53c-6b00-4251-b3e9-0f3310a0f7b5/video.mp4

## Entry 45
- ID: 10346
- Author: Umarbek
- Created At: 2026-05-30T08:13:17Z

### Content

I have started the Bill of Materials and completed it to the extent to which I could. There are many smaller materials/parts that still have to be accounted for (I've only put their names), but I am hoping that they could be better approximated by my teammate. I've reviewed the electrical components and their delivery dates, cheaper listings on other marketplaces, and updated the list to reflect the latest decisions on MIST. So far, it sums up to $371.94 USD, but it is expected to be higher. (I have also came to a realisation that the power supply for Raspberry Pi 5 we've been using is too weak, as RP5 required non-standard current. For now, current converter seemed to be the most elegant choice.)

Screenshot 2026-05-30 at 17.11.47.png

### Recording Links

- https://lookout.hackclub.com/api/media/a5833e07-74eb-45b6-acf5-84540a2b7a6e/video.mp4

## Entry 46
- ID: 10843
- Author: William
- Created At: 2026-06-01T06:38:27Z

### Content

### Mist Robot Arm: Development Log

I made the robot arm for Mist. Here is a breakdown of the design iterations:

**Version 1**

The v1 was way too bulky and ended up looking pretty bad. It used an 11kg servo motor at each joint. While powerful, this ended up making the arm almost as wide as the leg, which looked terrible.

**Version 2**

For the v2 (which I never fully finished), I decided to try to move all of the joints out of the arm itself by controlling it with a rope drive system. This worked great in theory, but it just concentrated the size issue further down into the arm, as it would interfere with the internal electronics if I tried to conceal it in the body.

**Current Iteration**

I went back to a servo at each joint, but this time I used micro servos. The reason I avoided this initially is that micro servos didn't seem able to hit the torque requirements without being absurdly expensive. After much searching, I managed to find a half-decent price, although they are still much more expensive and not as strong as the full-sized servos. 

**Next Steps**

* **Remaining Work:** The only things that remain are aesthetic and weight optimization, as well as sorting out which gripper to use. 

* **Gripper:** I currently have it set up as a modular system, so anything could be put there.


### Recording Links

- https://lookout.hackclub.com/api/media/b6f9eda6-308f-4d0e-a838-ee51ae80b7e2/video.mp4
- https://lookout.hackclub.com/api/media/ff0bda29-f026-4195-839b-19ed1f5cf061/video.mp4
- https://lookout.hackclub.com/api/media/d802a121-baac-4944-a09e-d6cbeafa0fc3/video.mp4
- https://lookout.hackclub.com/api/media/3b65ee98-45fb-4659-80c2-427ac2cd1a8b/video.mp4

## Entry 47
- ID: 12177
- Author: Umarbek
- Created At: 2026-06-07T02:21:40Z

### Content

It's been a while since we've last updated guide for setting up software on our robot. Therefore, I've written all of the instructions to get software part of the robot ready and running. We will test it out in the upcoming meeting with my teammate during build process. 

Screenshot 2026-06-07 at 11.19.46.png

### Recording Links

- https://lookout.hackclub.com/api/media/56e95f4c-89ac-445a-9889-17e6c9ad37d7/video.mp4

## Entry 48
- ID: 12201
- Author: Umarbek
- Created At: 2026-06-07T04:11:02Z

### Content

I have written and cleaned the code for controller and camera modules for MIST. Additionally, I've written some documentation for both with an example usage. Now, I can easily initialise and use controllers and cameras through simple go interface.

Below, there are screenshots of README's that capture simplicity and abstraction of using these packages now.

Controller:


Camera:


I will now move on to next modules. The goal for today is to have all of mist-os ready for review.

### Recording Links

- https://lookout.hackclub.com/api/media/0201fbac-ea3e-451e-a138-d805214f6223/video.mp4

## Entry 49
- ID: 12236
- Author: Umarbek
- Created At: 2026-06-07T09:19:23Z

### Content

While the screen module had a clean interface already, it for certain wasn't clean nor modular. I've modularised code for each eye and mouth types into separate folders and optimised speed of rendering for many features. Additionally, I've removed a lot of dead code. Here's MIST's happy face from changes I've made:



### Recording Links

- https://lookout.hackclub.com/api/media/e2b8680c-09e3-4473-96d8-31710879b633/video.mp4
- https://lookout.hackclub.com/api/media/c37768de-433a-4a1c-a737-5babb4a0f069/video.mp4

## Entry 50
- ID: 12265
- Author: Umarbek
- Created At: 2026-06-07T12:35:24Z

### Content

I have created a new version of text to speech module, which utilises the OS's built-in program in order to create and play an audio.

With a simple bash script, I have tested all of the sounds available on Mac on a short phrase. It worked out perfectly, and 

Testing on Raspberry Pi's Dietpi was of more trouble, but by creating audio files and exporting them into a folder which my own alternative of google drive shares to the internet, I was able to get the voice lines onto my device. Unfortunately, the voices in linux configuration were too basic. I have chosen one of the voices for now, but now there are plans on using neural-network based models or simple vocaloid of some sort.

The module is now ready and working, the package is usable and production ready.



### Recording Links

- https://lookout.hackclub.com/api/media/f5b67658-44a1-4395-bb0d-810dccae58e4/video.mp4
- https://lookout.hackclub.com/api/media/0068e534-4daa-42ce-b2f7-d08ad6805467/video.mp4
- https://lookout.hackclub.com/api/media/ae29fc2e-f836-425e-8ad5-391f9d409690/video.mp4

## Entry 51
- ID: 12283
- Author: Umarbek
- Created At: 2026-06-07T13:53:06Z

### Content

I've tested running LLMs on edge using Ollama. The hoped-for Gemma4:2eb turned out to be too large, nearly bricking my raspberry pi 5:8gb by filling out its ram and heating the CPU to the level of boiling water. As last reading before disconnect showed critical temperature, I dived into the box of cables to find my raspberry pi, and reboot it. Whilst waiting for the red light to turn green, I ran to the kitchen for ice, which I've used to cool the cpu down. (just realised that it's quite similar to pantheon.)



Gemma4:2eb was a total disaster, as I've started searching for other models. Qwen3.5:0.8b looked promising as it was the smallest model supporting images. Running it on raspberry pi, I got stable 74 degrees celcius and quite a few words per minute. It is promising. In order to use it, we will limit or disable thinking, and add cooling to the raspberry pi. 



All that's concerning is for the LLM not to take all the resources of the raspberry pi, as there are way more critical components to the system, such as sensor readings and actuator control. I should find a way to ensure that physical component control is prioritised over LLM.
I am also considering if getting something adjacent to Raspberry Pi AI HAT+ 2 or Coral AI accelerator would be a good idea. If budget allows, this could be the solution.

I have added guide for installation of Ollama and correct model for diet-pi. It is now updated and up on GitHub. Next, I will start creating harness/brain for our robot.

### Recording Links

- https://lookout.hackclub.com/api/media/13c74f3d-05cf-4dea-bc6a-d35280aff4a2/video.mp4
- https://lookout.hackclub.com/api/media/7bfc6e0c-6d38-4681-a48a-18864ea3f6f2/video.mp4

## Entry 52
- ID: 12542
- Author: William
- Created At: 2026-06-08T17:10:30Z

### Content

Alright, so I finished up the gripper and arm assembly as a whole. I still need to do some weight reduction, although a lot of that can be accomplished with slicer tweaks. I didn't record it, but I got my second 3d printer up and running with some new firmware, which will let it go a whole lot faster. Still working on tuning it. For the gripper, I went with a worm drive to a normal 6mm geared motor; even the smallest servo was too big to fit, so I went with the smallest motor I could find. I'm hoping that I can use the current draw to detect force so it can know how hard it's holding something. The worm drive also makes it not backdriveable, so that's pretty cool. The grippers are compliant, so they can grip a multitude of shapes. I'm going to keep working on maintaining and upgrading the printers cause theyll need it. Also working on making a phone stand to record IRL.




### Recording Links

- https://lookout.hackclub.com/api/media/a7d1f5be-a928-474f-a2b8-96d8435a8d1d/video.mp4

## Entry 53
- ID: 12759
- Author: Umarbek
- Created At: 2026-06-09T13:59:20Z

### Content

To be completely honest, I had my wisdom tooth taken out this afternoon after school, and pain has greatly reduced my capacity to do work ("Energy" as by physics definition, lol?). Due to anesthesia, my brain is foggy, but here's what we got:
1. A beautiful orchestrator/harness for the local LLM.
1. A confirmation that local models are too dumb (yes, I'm referring to you, Qwen2.5vl:3b, Qwen3.5:0.8b, and moondream.) As my teammate has proposed yesterday, we will (unless some genius will invent a way to make smaller models substantially smarter, helping me with this project and crippling Ai industry in the background) have to fine tune it on our tool-calling.



### Recording Links

- https://lookout.hackclub.com/api/media/b7faaf59-ce58-4164-af3a-543abe37c29d/video.mp4
- https://lookout.hackclub.com/api/media/f534824b-13ac-4661-99e2-a847e2e1e7a5/video.mp4

## Entry 54
- ID: 12981
- Author: Umarbek
- Created At: 2026-06-10T10:05:45Z

### Content

I've written documentation on how to activate I2C protocol on raspberry pi with dietpi. (I am now realising how many steps does MIST take to configure, writing an automatic script later in time would be a good choice.)

I have encountered many many issues with our current chosen model of the IMU, which includes driver issues, protocol issues, wiring issues and more.
Here are the options I've considered:
We could do one of the following:
1. Limit amount of data we get, and stream more primitive readings to some part of the OS as a peripheral, which will be read by our singleton.
2. Have a contained python script that will stream all the data to our Go singleton
3. Just get another IMU (MPU-6050 seems like a great choice tbg) (way cheaper as well)

And honestly, since we haven't started building her yet, we can at no loss choose option 3, saving us a lot of pain and headache in the future. So far, MPU6050 seems like a good option with great support (and surprisingly lower cost). I will now try adjust the wiring (I wrote most of the updated script). 



Now, in writing this, I realise that the IMU data I'm working with are all random numbers. I should also add translator capabilities to turning these numbers into m/s and other SI units. + I'll have to write streaming option rather than function calling for real-time robot body processing later.



### Recording Links

- https://lookout.hackclub.com/api/media/d91175b3-a419-483f-afd4-6bdba9b7a778/video.mp4

## Entry 55
- ID: 13138
- Author: Umarbek
- Created At: 2026-06-11T03:08:45Z

### Content

I have finished working on the IMU package. I have written clean, modular code which (should) provide an easy way to work with the physical sensor.



It is important to say, however, due to not having physical hardware on myself right now, it is uncertain whether this code would work. I've added configuration information on the main README and few methods of testing if everything is correctly connected and functioning. 

I have also updated the wiring guide on Figma, replacing the old IMU to the new one. (after copying from an online guide I found, at the end, I've double checked-with Gemini, and it said everything is correct, so...)

So far, this is the list of packages in the repository: 
  + camera
  + controller
  + screen
  + voice
  + imu
  ~ ai
  - body
  - hand
  - brain
  - eyes
  - maths
  - main
, and I will probably now go to the body module, working on controlling of the servos and brushless motors as well as finishing the wiring I've started a while ago.



### Recording Links

- https://lookout.hackclub.com/api/media/99ee39db-fea8-4c5a-a9ab-adf71ecee4c2/video.mp4
- https://lookout.hackclub.com/api/media/cb45e654-df09-42f0-baec-a365229295a0/video.mp4
- https://lookout.hackclub.com/api/media/ff738864-4dea-4f67-98ef-abfa4447e220/video.mp4
- https://lookout.hackclub.com/api/media/49097bdb-58df-40e6-8e99-43562d5627e1/video.mp4

## Entry 56
- ID: 13200
- Author: Umarbek
- Created At: 2026-06-11T10:46:41Z

### Content

I have created a module for servos and motors! This was surprisingly easy to be honest, and controlling them is rather fun than tedious. 



I think it is mainly due to Esia choosing a popular variant which has a good documentation and community support.

The PCA9685 provides a clear minimal interface, making development enjoyable!



### Recording Links

- https://lookout.hackclub.com/api/media/7259157b-d89a-4b31-b6e3-c608d9174642/video.mp4
- https://lookout.hackclub.com/api/media/9a7b8910-b7c3-4ef3-878a-d0689df26387/video.mp4
- https://lookout.hackclub.com/api/media/cce0d27e-6592-46a8-b883-2cebafdc7ebe/video.mp4

## Entry 57
- ID: 13226
- Author: Umarbek
- Created At: 2026-06-11T13:56:05Z

### Content

I have worked further on the wiring for MIST, specifically focusing on power and its distribution; it was a challenge. It is uncertain what specific hardware to use for some parts such as Battery, Power Distribution Board, Buck Converters.

Additionally, it seems like we've been using wrong motor type for the job, and I only now came to a realisation on the difference between aerial motors and ground motors, with aerial motors having nearly no torque. Remembering my previous conversations and looking into CAD model (why navigation in CAD with a trackpad is so challenging for no reason? is it really hard figure it out like Blender did decades back?), my friend and teammate has implemented gear reduction mechanisms, but the question is: is this complexity and uncertainty justified or should we just use a ground motor?

(Btw, I'm unsure if it applies to everything but I've noticed that harder it is to wire something, the easier it is to program it and vice-versa.)

It is still unfinished, and the wiring must be reviewed, but the progress is honestly great! Here's the progress so far:



### Recording Links

- https://lookout.hackclub.com/api/media/e03a89be-4320-4bd8-8cf8-6a84bc3276c6/video.mp4

## Entry 58
- ID: 13674
- Author: Umarbek
- Created At: 2026-06-13T08:14:19Z

### Content

In earlier designs of methods of controlling MIST, there were too many different options. Thus, there was a proposition to use a singular button in a morse-code style in order to expand upon available inputs. (Currently, it is to be used in controlling screen types.)



Creation of telegraph module in golang was quite engaging, and seeing the results felt magical? Turns out, after fine-tuning, hard-coded time durations for difference between dot and the line as well as idle time until the character is recorded it works flawlessly!



### Recording Links

- https://lookout.hackclub.com/api/media/d6c60a16-7392-4168-9568-b9d8c83229c3/video.mp4

## Entry 59
- ID: 13720
- Author: Umarbek
- Created At: 2026-06-13T13:36:01Z

### Content

I have finally embarked on a journey of actually figuring out MIST's higher-level physical controls. But before that... of course, I have decided to rewrite the structure of actuators' code. 

Now, instead of having a large object where one must have all of the robot's motors at once in order to control a singular servo on the head, it is possible to create a singular actuator controller, which can then be passed as an argument to NewServo(), NewMotor() functions to have a pointer and methods for a specific motor. 

This significantly simplifies the process of working with the hardware, keeping everything modular and safe: no servo functions available on motors anymore!)

I have also thought more on how to map controls from a gamepad onto movements in MIST. I was struggling with mediocre-limiting methods until I remembered how much I love drones! And how closely MIST resembles one! Therefore, it is now decided. 

For the higher level body functions, I have implemented one for the head, and partially for wheels (the actual way of controlling mist was important here, so I steered off a little as you see.) I have also realised that we could get more data from the controller from its gyroscope and accelerometers! 

Next, I will forget about the body for a little, implementing the functionality of gyro+accel read on a controller, after which I'll come back to the body, finishing the head off, and continuing with wheels, knees, and hand.





### Recording Links

- https://lookout.hackclub.com/api/media/280d6d38-8387-4936-9191-2e566fb74599/video.mp4
- https://lookout.hackclub.com/api/media/80d52b06-6a14-4ccf-9572-3f7f793cf8a3/video.mp4

## Entry 60
- ID: 13733
- Author: Umarbek
- Created At: 2026-06-13T14:36:51Z

### Content

I have worked on getting the accelerometer and gyroscope data from the controller. The stable version of sdl I was using turned out to be too old, requiring me to update to the new alpha version, which stalled. In a dubious debugging session, I've figured out that the new version has switched from iterating pointers to values directly. Thus, updating the switch statement by just removing the *'s has fixed all of the problems. 



### Recording Links

- https://lookout.hackclub.com/api/media/f3f1865a-eff5-4367-a71a-118005a6befc/video.mp4

## Entry 61
- ID: 13878
- Author: Umarbek
- Created At: 2026-06-14T03:39:34Z

### Content

I have finished upon figuring out the controls and writing code for wheels! It will be controlled in this way: 

R3:
- forward-backward: movement, riding in that direction by reversing motor direction
- right/left tilt: rotation on place (left back right forward and wise-versa)
L3:
- forward-backward: up-down (controlled from the servos on knees)
- right/left: turning (forward legs turn up to 30 degrees right/left, like in a car)
(Gemini wrote a simulation from which my brother and I have tested the controls, and it seems to be perfect!)



I have also updated the motor class from the actuator module to support bidirectional movement (it only worked for movement in one direction before.) Without physical hardware on my hands, it is hard to confirm if the codebase actually works, but we'll be hoping for the best. 

Now, when choosing a new ESC Control, we must ensure it supports bidirectional throttle. 



### Recording Links

- https://lookout.hackclub.com/api/media/d9819b1d-a102-4f9f-b75d-0a7de2064f19/video.mp4

## Entry 62
- ID: 13887
- Author: Umarbek
- Created At: 2026-06-14T04:25:05Z

### Content

In working on the knees (which is a headache of its own 8 servos worth), I got distracted a little, and worked a little on what MIST's shot for the zine might look like. I've exported the FreeCAD model to blender (unfortunately the mesh was ugly and unusable, leaving me with the straight standing pose unable to rig or even simply move it.)

I applied a glass shader, created a simple 3 point light setup and rendered it, getting this masterpiece:

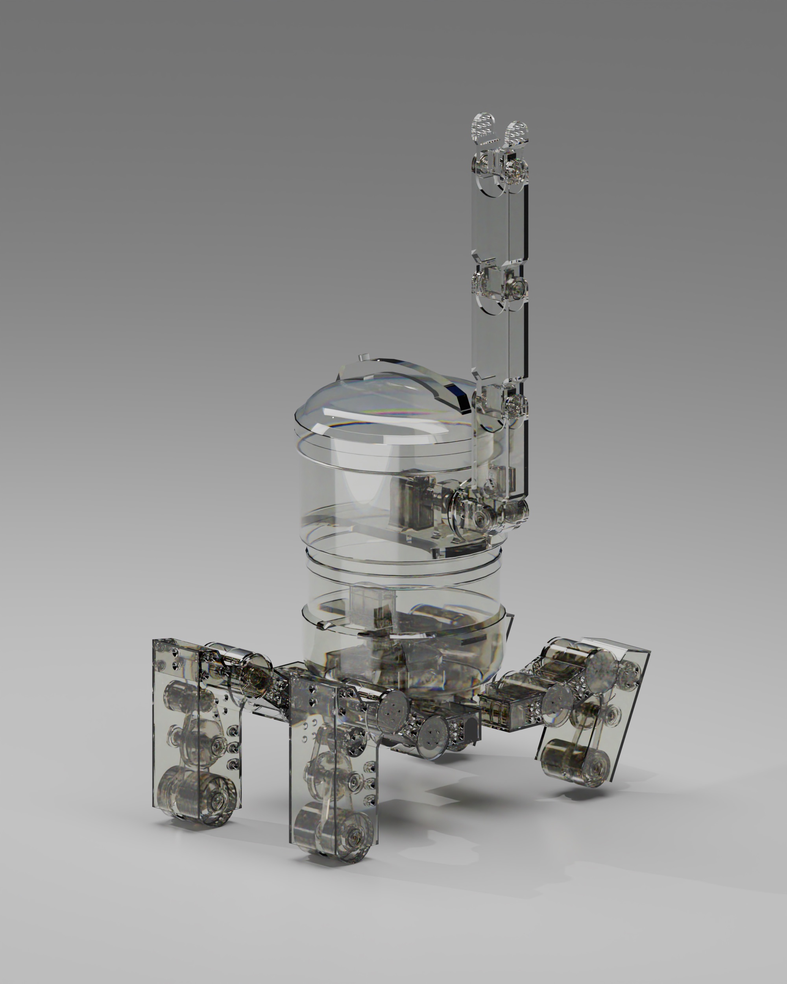
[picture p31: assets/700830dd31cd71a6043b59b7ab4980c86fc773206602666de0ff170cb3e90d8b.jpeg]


I've put settings on low in order to see approximately how will it look; I will later render it at better quality with more passes (in order to avoid using denoise and making it blurry.). Additionally, this is an outdated model, and I will replace it with articulated final model from Esia (hopefully) tomorrow.

### Recording Links

- https://lookout.hackclub.com/api/media/d80e6c78-49a5-45c5-8771-ec745aeba7b4/video.mp4

## Entry 63
- ID: 13914
- Author: Umarbek
- Created At: 2026-06-14T08:15:47Z

### Content

The hardest part of coding MIST is now finished!!

The 8 servos responsible for the knees/legs seemed as an impossible challenge where I will struggle a lot. Thanks to the YouTube and couple great creators, I have understood the mathematics behind forward, and backward kinematics sufficient enough for a joint of 2 degrees of freedom.





Now, MIST tilts forward and backward, and can go up and down in height. I have now remembered that lastly, I need mechanics to turn right and left. I will work on it afterwards.



### Recording Links

- https://lookout.hackclub.com/api/media/6b293bb0-c594-4091-bba1-9f254aef85d2/video.mp4
- https://lookout.hackclub.com/api/media/cb53d225-e268-41be-a431-104429ae88ca/video.mp4
- https://lookout.hackclub.com/api/media/c4534e6f-52d1-4d09-95dd-e5d77fecacbe/video.mp4

## Entry 64
- ID: 13917
- Author: Umarbek
- Created At: 2026-06-14T08:37:23Z

### Content

After working with all of the complex modules, animating hips was a little too simple. It just required rotation of two servos from a singular vector input, which I've implemented. Nothing special, just a hip module finished.

Next, I will implement the hand module, after which, I will assemble everything into body class, which will then be controlled by the brain, which finally connects controller inputs to the actuators, making MIST's code complete!

I have also noticed how we've ran out of ports on PCA9685,  we should resolve it later, while making the wiring/assembly guides. For now, I've added it to an invalid port number:



Screenshot 2026-06-14 at 17.32.31.png

### Recording Links

- https://lookout.hackclub.com/api/media/346da6c9-8b0a-4f8e-ad0f-b579eb5a3252/video.mp4

## Entry 65
- ID: 13959
- Author: Umarbek
- Created At: 2026-06-14T12:20:06Z

### Content

Initially, I was planning to work upon the last, hand module, but it is quite hard to understand what William has designed with black magic. Therefore, I skip this step for now, skipping to body module right away.



I have created a body module, that combines controller inputs and all of the actuators in order to finally make MIST move! It's been a long way until here and there's a little more left, mainly combining the screen inputs, and camera to the body module.

Further, if sufficient time is given, I should add intelligence layer on top. I completely give up on local LLM models: they are too dumb (though I will probably add whisper for speech to text and embedding Gemma through Ollama for tiny local database and facial recognition.) These three things should allow to have autonomous MIST, though who knows how much tokens will this setup burn through.

### Recording Links

- https://lookout.hackclub.com/api/media/b5b0914e-1c50-4ca3-95fd-2266c3870ef9/video.mp4
- https://lookout.hackclub.com/api/media/0fd0d475-25bc-49f8-b997-21012fdee4af/video.mp4

## Entry 66
- ID: 13989
- Author: Umarbek
- Created At: 2026-06-14T15:05:26Z

### Content

The face module is pain module! 
I am tired of wasting so much time on designing each facial feature one by one. I have come to understanding that I could use an SVG library to design these on my own and just displaying them in screen module. I am taking a rest from the screen module for now...

With creating of a zine! This is a prototype of a zine for now, which uses the earlier concept art of a transparent glass MIST. I've designed it along other peers in a slack huddle, getting some feedback in the process.

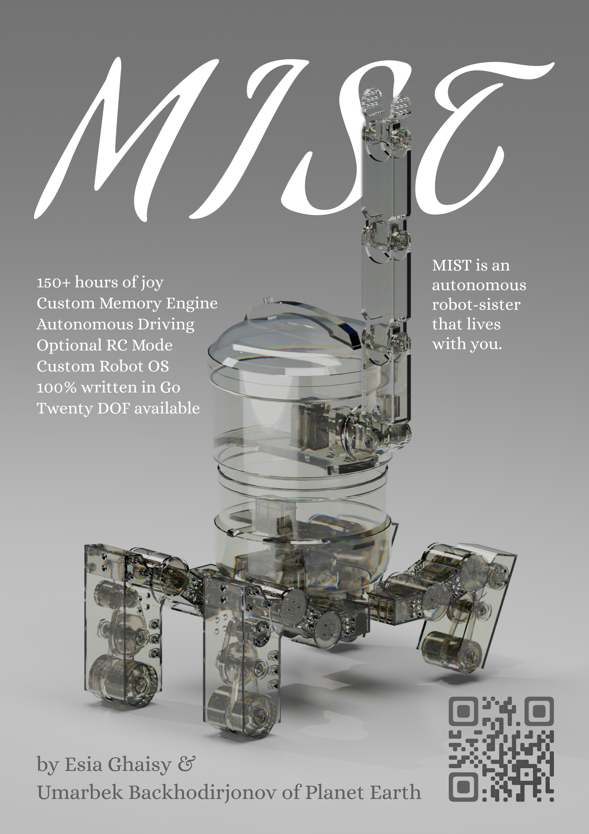
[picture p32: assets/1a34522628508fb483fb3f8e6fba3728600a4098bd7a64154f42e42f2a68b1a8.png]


### Recording Links

- https://lookout.hackclub.com/api/media/4c7b7e78-86d3-49ac-85eb-08d4f0c67e25/video.mp4
- https://lookout.hackclub.com/api/media/33043589-afa3-423f-891b-8b3dd3c9966d/video.mp4

## Entry 67
- ID: 14153
- Author: Umarbek
- Created At: 2026-06-15T03:00:25Z

### Content

The codebase for MIST is 100% complete, and (should be) functional!! The satisfaction of opening dozens of modules in the main.go and brain.go is indescribable.



In fact, everything is so elegantly modularised that this is all that's needed from main.go:



### Recording Links

- https://lookout.hackclub.com/api/media/8ba2a7b3-8ee7-487d-ad0d-4bdd8d6f8f81/video.mp4

## Entry 68
- ID: 14176
- Author: Umarbek
- Created At: 2026-06-15T05:35:58Z

### Content

This is the continuation of creating a brain module for MIST. It is a continuation of the previous journal. For the photo, I will just add a screenshot of brain module. 



### Recording Links

- https://lookout.hackclub.com/api/media/43fe7301-b290-4b3f-9af7-63f3ac0ac494/video.mp4

## Entry 69
- ID: 14179
- Author: Umarbek
- Created At: 2026-06-15T05:37:54Z

### Content

I have completed wiring schematics for the base robot (all excluding the arm). We already had a quite good scheme but it was all over the place; now, everything is colour-coded and available in a singular image with port allocations.

Circuit Guide.png

### Recording Links

- https://lookout.hackclub.com/api/media/cb6ad4ac-8ec8-426e-8631-93b50476c625/video.mp4

## Entry 70
- ID: 14273
- Author: Umarbek
- Created At: 2026-06-15T16:49:29Z

### Content

This was supposed to be part of the previous recording, where I have finished the wiring. I forgot to stop the recording before typing in and submitting the previous journal. I will add the same diagram as the last time: 



### Recording Links

- https://lookout.hackclub.com/api/media/3bec42fa-f9be-48d5-a74e-e7a8c68433b7/video.mp4

## Entry 71
- ID: 14300
- Author: Umarbek
- Created At: 2026-06-15T19:05:32Z

### Content

I have been doing last touch up changes to the MIST before submitting it for review. I've touched upon few small details in wiring, did the whole exporting, file conversion black magic, and rendered the last version of MIST in Blender, now with updated colour  palette. 

I also made the last iteration of zine!



### Recording Links

- https://lookout.hackclub.com/api/media/8088257b-fb5a-4517-8af7-9f07ef3d676d/video.mp4

## Entry 72
- ID: 14352
- Author: Esia
- Created At: 2026-06-16T01:03:07Z

### Content

During this stage, I caught up with Umarbek and we explored different options of cutting down on servos to simplify the project and ensure we'd be on track to get it done.

Screenshot 2026-06-15 175314.png

Ultimately, we figured we'd be able to get rid of two motors by removing the hip motors in the back, chunky legs and make them entirely static. This would enable us to package the other hip motors with more freedom and reduce overall design, build, and programming strain across the board.



### Recording Links

- https://lookout.hackclub.com/api/media/74dbb1a4-3b24-4c02-a656-a198db114615/video.mp4

## Entry 73
- ID: 14364
- Author: Esia
- Created At: 2026-06-16T02:08:06Z

### Content

Here I took some time to design the hip mechanism for the legs that I had yet to develop. The two legs already developed and mounted were stationary with a bracket that when mounted, positioned them in the neutral position facing directly forward, balanced across the center of the robot. This way, I had eliminated the need to worry about the bias from the weight of the back legs as their weight canceled each other out and they could instead act as a stabilizer for the front, skinny legs.

As such, I had significant freedom in working on the hips and I was able to come up with a coaxial hip design that utilized two servos, each for a hip and a leg.



It was relatively difficult to package two different coaxial hips on top of each other with a direct servo connection so I chose to instead position the servos off to the side and belt the servos onto each hip.

Then, I had to make the decision to gear down the servos at a ratio of 27:67, decreasing the servo's range by 40% whilst increasing it's resolution by the same amount. More importantly, we achieved a 40% increase in torque, allowing us to utilize the knee servo model in the hips as well.

Screenshot 2026-06-15 185518.png

With two legs mounted, and the hips for the final two legs developed, I moved onto finishing up the final set of legs and mounting them onto the hips.

### Recording Links

- https://lookout.hackclub.com/api/media/83f1eb65-4454-4505-9236-3945f2565199/video.mp4
- https://lookout.hackclub.com/api/media/f8b6ff78-c768-4f0a-bdb7-fe616739c9b2/video.mp4

## Entry 74
- ID: 14369
- Author: Esia
- Created At: 2026-06-16T02:24:20Z

### Content

Starting on the third leg, I made a huge mistake in my approach.

Initially, my logic was that I'd make the "skinny" set of legs an entirely scaled down version of the chunky legs. With this, it meant my joints would need to become smaller, and as such I designed a leg entirely for these smaller servos, downsizing the leg by 25% but losing approximately 75% of the torque I had before to rotate the knees going from the MG996r with 11kg/cm of torque to the MG92B with 3.5kg/cm of torque.

PTC Creo Screenshot 2026.06.15 - 19.13.22.40.png

After I realized my mistake and that the robot would not function with _weak knees_ I realized my better option would just be to snatch what I already have from the other legs and only redo the final leg segment as it had the most volume that I could take away from and give the illusion that the front set of legs is overall smaller. So, I chose to do that instead.

PTC Creo Screenshot 2026.06.15 - 19.21.05.14.png

### Recording Links

- https://lookout.hackclub.com/api/media/390043bf-2996-4aee-858c-d74744e54c56/video.mp4

## Entry 75
- ID: 14374
- Author: Esia
- Created At: 2026-06-16T02:57:09Z

### Content

Here I honestly spent a lot of time jumping between things. I went from designing the last legs to integrating them into the hips and body whilst also editing the model of each leg, gearing down the motors some more and redesigning the wheels to support a layer of flexible SEBs filament in order to not _crack_ upon rough contact or blunt force.

Here's some photos of the stuff I was working on:

Wheel sleeve: 
PTC Creo Screenshot 2026.06.15 - 19.39.03.61.png

Trying to figure out how to design tire treads:
Desktop Screenshot 2026.06.15 - 19.49.40.48.png
Desktop Screenshot 2026.06.15 - 19.52.41.87.png

Mirroring the complete 3rd leg to create the 4th and final leg: 
PTC Creo Screenshot 2026.06.15 - 19.43.18.98.png

Integrating legs into hip design and hips into body:
Desktop Screenshot 2026.06.15 - 19.55.51.27.png

### Recording Links

- https://lookout.hackclub.com/api/media/d4fa9410-b54c-4d60-9c6d-766f5bab2c7e/video.mp4

## Entry 76
- ID: 14375
- Author: Esia
- Created At: 2026-06-16T03:15:57Z

### Content

I finished up the tire treads using some new cool Creo features I learned:




And spent like two hours getting MIST's holes ready for hardware (ensuring tolerances are right, chamfers are right, etc.)

PTC Creo Screenshot 2026.06.15 - 20.11.22.42.png

That's like all I did for two hours. It takes too much time to mount stuff. Idk.



### Recording Links

- https://lookout.hackclub.com/api/media/c2666c3a-642f-4bf8-bb09-4294c9b85190/video.mp4
- https://lookout.hackclub.com/api/media/49c617d4-8280-4ad7-bd09-ccdec21e606f/video.mp4
- https://lookout.hackclub.com/api/media/5d425d0f-c2d1-44bf-87df-823e313ed28b/video.mp4

## Entry 77
- ID: 14441
- Author: Esia
- Created At: 2026-06-16T03:35:14Z

### Content

I mounted around 90% of the hardware that I left for the end of the project (mostly screws and nuts) with the 10% remaining having been the hardware on William's arm which I was still figuring out if him or I would be taking care of it.

I sourced all of the screws and nuts from McMaster-Carr which has a wide variety of hardware:


I spent all of the time during this recording cycling between McMasterr and Creo resizing holes and exporting screw models for my use where I excruciatingly hand assembled each and every screw and nut onto MIST across the entire assembly.

to spend 6 hours mounting screws and nuts.png

### Recording Links

- https://lookout.hackclub.com/api/media/51c69037-bf4a-466c-9155-d2f81fe52ec3/video.mp4

## Entry 78
- ID: 14449
- Author: Esia
- Created At: 2026-06-16T03:49:16Z

### Content

Here I finished mounting all the hardware entirely. All screws and nuts on the base model without electronics had been assembled, including on the arm, and I moved onto assembling the electronics.



### Recording Links

- https://lookout.hackclub.com/api/media/bd758851-1d0e-45a6-8e8b-6b8982dacbd4/video.mp4

## Entry 79
- ID: 14451
- Author: Esia
- Created At: 2026-06-16T04:01:44Z

### Content

After some intensive research for CAD models matching the electronics we're using, I was able to find some accurate models to mount onto MIST. The first two electronics I tackled were the Raspberry Pi and screen, which after a bit of research I discovered could actually and are supposed to be mounted on each other directly, following a connection directly to the Raspberry Pi that streams both power and video to the screen.




The first version of the mount that I designed: 


After some feedback from Umarbek I also rounded the corners on the case and it's mount, giving MIST a more premium look, as though she's wearing a visor:



### Recording Links

- https://lookout.hackclub.com/api/media/0b746458-c697-45b8-b6ad-2de9df7d19e6/video.mp4

## Entry 80
- ID: 14454
- Author: Esia
- Created At: 2026-06-16T04:17:43Z

### Content

Approaching the end of the design process, with the electronics selected and hard work already done from past meetings with Umarbek and William I really just had them remaining to mount:

MPU6050
PCA9685 x2
Mini PDB x2
Large PDB
UBEC x2
Camera
Lipo Battery
ESCs (motor controllers) x4

Aside from the electronics, I also added some finishing touches and polish that gave more life to the model and added to the accuracy and faithfulness to the show:

Screenshot 2026-06-15 210328.png
Screenshot 2026-06-15 210404.png

I also made the lid be removable and screw back on because it was the simplest way I figured we'd access the electronics inside MIST:

Empty brain MIST


Anyway, here's some photos of where I mounted the electronics:

PCA9685 x2
Mini PDB x2
Large PDB
UBEC x2
Lipo Battery




Camera


MPU6050


ESCs (motor controllers) x4
Mounted with red mounting tape to the walls of MIST's legs.



Anyhow, that's all. Mist's CAD is done. I'm ready to work on finishing up the github repository, BOM, and wiring/assembly guides to get it ready for submission.

### Recording Links

- https://lookout.hackclub.com/api/media/e1031377-7b03-488f-8241-d773cc05c4b3/video.mp4

## Entry 81
- ID: 14459
- Author: Esia
- Created At: 2026-06-16T04:40:38Z

### Content

I worked solely on getting MIST ready for submission during this entire recording, minimizing costs in the BOM, getting visual shots of MIST for our zine, ensuring our wiring diagram is complete, to including all of our documentation and relevant info in the github.

Currently, our project is in a state where we can submit it with complete firmware, CAD, and a zine, however I am looking toward improving the zine with more technical info on what MIST does as well as minimizing costs on the BOM to prevent rejection on the basis of cost.

Here's some pictures of our current documents and models:




### Recording Links

- https://lookout.hackclub.com/api/media/8ee33869-2e35-4fff-9d00-59d27895acde/video.mp4

## Entry 82
- ID: 14771
- Author: Umarbek
- Created At: 2026-06-17T15:08:13Z

### Content

Unfortunately, the super-duper cool transparent MIST render wasn't something one of the reviewers liked, which they've told us informally as the actual review of our project hasn't started yet. Thus, we're completely redesigning the zine now, with many new elements, explanations and less fancy design. Here is the update: 



### Recording Links

- https://lookout.hackclub.com/api/media/2e334a14-49ef-452c-aabe-879cdb33a253/video.mp4
- https://lookout.hackclub.com/api/media/5186ec76-eb80-4fa4-a67e-8586afc211e8/video.mp4
- https://lookout.hackclub.com/api/media/60a6d17b-3786-42c4-9b10-2efec44f261b/video.mp4

## Entry 83
- ID: 14774
- Author: Esia
- Created At: 2026-06-17T15:38:09Z

### Content

Umarbek and I essentially entirely redid our zine in a SINGLE sitting to better align it with project requirements, particularly in showing how our project works and what exactly it's purpose is.

Initially, this is what our project's zine looked like:


It looked breathtaking, but honestly it was unclear what our project was technically speaking. After this was brought to my attention by a fallout reviewer Sam Liu I prompted that Umarbek and I redesign our zine. Here was our first two attempts at a redesign, encapsulating more technical info and explaining how our project works:

Screenshot 2026-06-17 020432.png
Screenshot 2026-06-17 081001.png

We didn't know where we were going with the design, we just knew we needed a way to see the robot and it's inner workings at the same time. We accomplished this by using two layers, one with the electronics over a layer of just MIST.

It wasn't terrible but it lacked a cohesive theme and we couldn't decide on whether we wanted it to appear toony with thick outlines or bold similar to that of a Times magazine:


Liking how the outlines looked though, we leaned toward a toony style and tried to incorporate this in our next iteration: 
Screenshot 2026-06-17 040559.png

With this addition, our zine started to stop looking like a mess and more like a hackclub magazine. A few more iterations and some 3 hours later we came up with this:

Screenshot 2026-06-17 080923.png

and this:

Screenshot 2026-06-17 071353.png

Which we mildly changed into our final zine iteration:


With that, MIST was complete! Thank you for following our journey if you've read up to here. Check out MIST on our github: https://github.com/flushloll/MIST



### Recording Links

- https://lookout.hackclub.com/api/media/9e6db43e-c138-487f-a930-4d6c7f7d6e47/video.mp4

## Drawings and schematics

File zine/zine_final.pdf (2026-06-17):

# by Esia Ghaisy, William Nzive &

# M I S T G

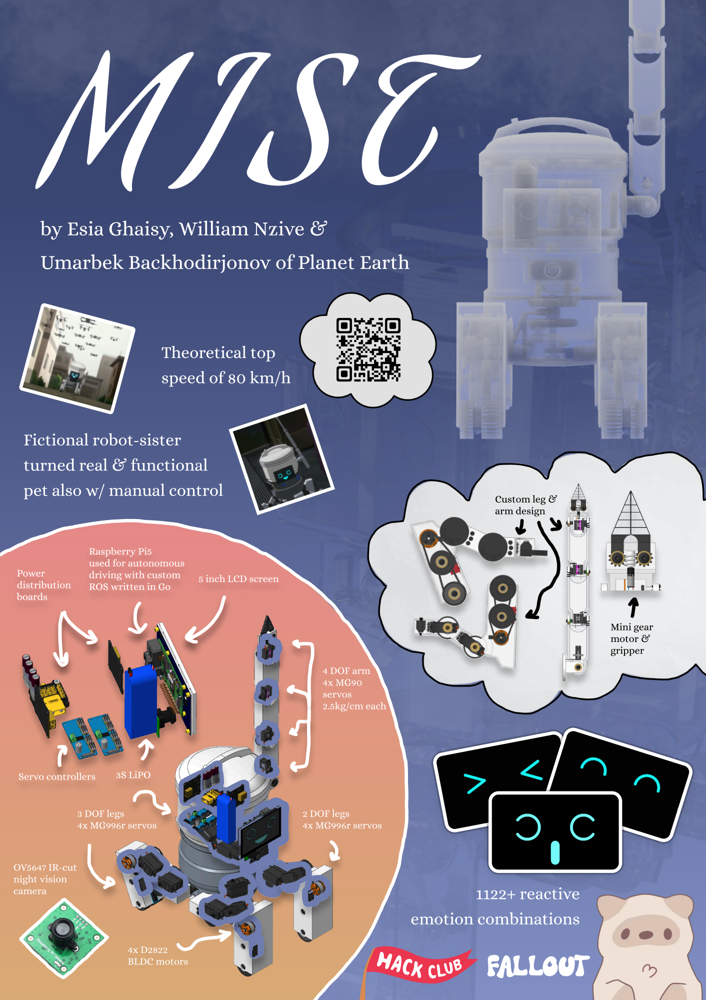
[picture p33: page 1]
Theoretical top; Power; distribution; boards; Raspberry Pi5; ROS written in Go; 5 inch LCD screen; 4 DOF arm; servos; 2.5kg/cm each; Custom leg &; arm design; Mini gear; motor & gripper; Servo controllers; 3S LiPO; 3 DOF legs; 4x MG996r servos; OV5647 IR-cut; night vision; camera; BLDC motors; 2 DOF legs; 1122+ reactive; emotion combinations

Umarbek Backhodirjonov of Planet Earth

speed of 80 km/h

Fictional robot-sister

turned real & functional

pet also w/ manual control

used for autonomous

driving with custom

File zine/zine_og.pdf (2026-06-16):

# M I S T

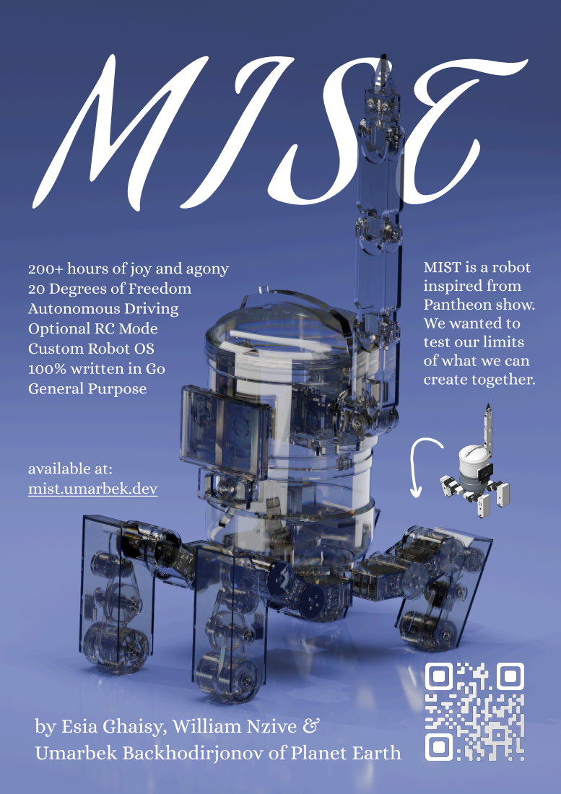
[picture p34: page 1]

200+ hours of joy and agony

MIST is a robot
inspired from
Pantheon show.
We wanted to
test our limits
of what we can
create together.

20 Degrees of Freedom

Autonomous Driving
Optional RC Mode

Custom Robot OS
100% written in Go
General Purpose

available at:
mist.umarbek.dev

by Esia Ghaisy, William Nzive &
Umarbek Backhodirjonov of Planet Earth

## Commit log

2026-06-03 uploaded current state of CAD for burnout
    [Case.SLDPRT, Output Shaft.SLDPRT, Pan Head Cross Screw M1.6.SLDPRT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]
2026-06-07 production ready camera and controller modules
2026-06-11 imu package finished
2026-06-11 actuator package finished!
2026-06-13 improved upon actuators and started the bodywork
2026-06-13 updated controller! now supports sensors such as accelerometer and gyroscope :D
2026-06-14 updated actuator code to support bidirectional movement and created wheel Drive() function for R3 joystick.
2026-06-14 knee and leg modules finished!
2026-06-15 added schematics guide
2026-06-15 updated schematics guide
    added additional pca9685, pdb, and clarified wording, wire assembly, and wire gauge
2026-06-15 updated CAD model to latest and final version
    everything needed to understand and assemble the robot is in the CAD now
    [2.0_PIN_HEADER.SLDPRT, 2xUSB_2.0_PORT.SLDPRT, 2xUSB_3.0_PORT.SLDPRT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]
2026-06-15 uploaded STP of latest and final version of CAD
    [0002_prt.stp, 10-32_screw_eighth_inch_prt.stp, 10-32_screw_halfinch_prt.stp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]
2026-06-15 removed old schematics guide
2026-06-15 updated readme to include new zine & schematics guide
2026-06-15 uploaded old zine & schematics back
    it was stupid to delete them
2026-06-15 clarified PCA9685 ground connection
2026-06-15 added some assembly info & future contributions suggestions
2026-06-15 added some wiring explanations & safety tips
2026-06-15 wording change in wiring section
2026-06-15 motor selection images
2026-06-15 current mist journal entire log
2026-06-15 added math section to readme with motor specs
2026-06-15 PDF version of BOM
2026-06-15 deleted BOM.pdf cause wrong info
2026-06-15 correct BOM.pdf upload
2026-06-15 BOM.pdf rename
2026-06-15 trying to display BOM pdf
2026-06-15 trying to display BOM pdf
    Update BOM link formatting in README
2026-06-15 trying to make BOM link large and clickable at the same time
2026-06-15 adjusting formatting of BOM link
2026-06-15 BOM pdf link works
2026-06-15 Added BOM csv to readme
2026-06-15 uploaded standalone stp file instead
    previous version with seperate parts was taking forever to load
    [0002_prt.stp, 10-32_screw_eighth_inch_prt.stp, 10-32_screw_halfinch_prt.stp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]
2026-06-16 most up to date (and final? i believe) BOM
    [BOM.csv]
2026-06-16 also updated and final? i believe BOM.pdf
2026-06-16 new model with extra PDB
    [mist-asm.stp, mist_asm.stp]
2026-06-16 reduced cost in BOM by ~$200
    [BOM.csv]
2026-06-16 bom interactable pdf -> bom pdf
    name was redundant
2026-06-19 reorganized BOM files and STP file
    [BOM.csv, mist-asm.stp]
2026-06-19 updated BOM links in readme
2026-06-19 fixed export glitch
    the exported stp file had some odd part placement glitches that i fixed by modifying the export settings
    [mist-asm.stp, mist_asm.stp]
